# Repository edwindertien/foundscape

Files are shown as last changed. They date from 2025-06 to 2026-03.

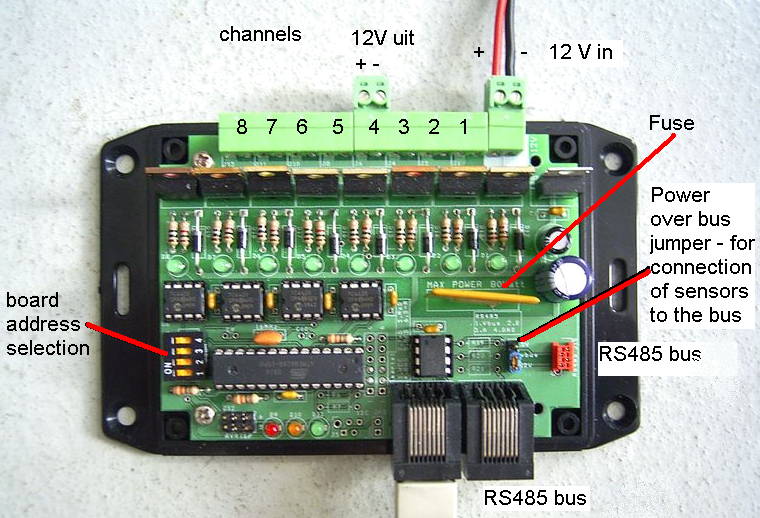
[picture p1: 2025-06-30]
atmegaDimmer/print.png

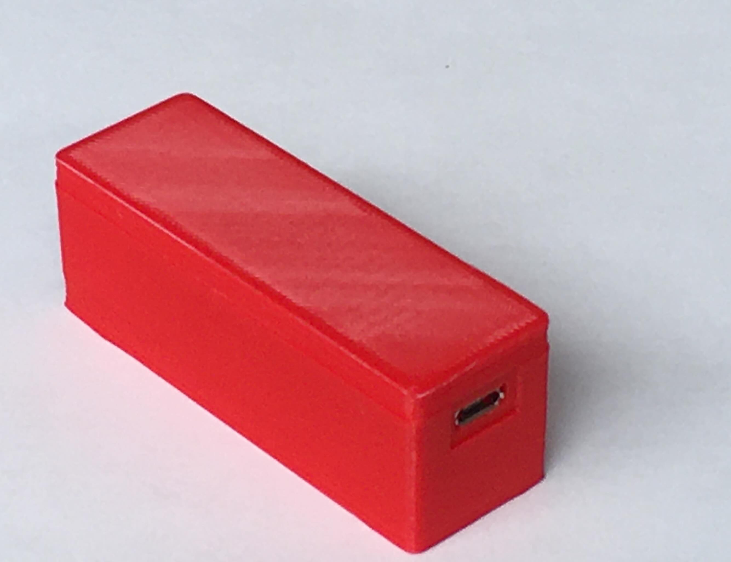
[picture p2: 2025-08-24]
images/RS485-midi-back.jpg

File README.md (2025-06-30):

# foundscape
midi control of things that tap and go boink. The basic structure consists of a midi-interface that takes data from Ableton (or similar) and sends events to 'dimmer cards' - being called like that because initially they mostly controlled LED light. 

Two behaviours exist on the main board right now which can be set using a small dip switch: either pulse-lenght or pwm duty cycle as third 'velocity' argument in a MIDI command. 

current version (still in operation) uses an ATmega328 (started out with the ATmega8 and then the ATmega88 in WinAVR. now it uses the Arduino environment). In the meantime a version has been made using Teensy, but has not been further pursued / produces (when Teensies were made of nonobtanium). On the wishlist a new version with pico

## modules
- [actuators](./actuators/) 3D printfiles for solenoid holders
- [atmegaDimmer](./atmegaDimmer/) first generation dimmer/control box, using RS485(dynamixel) protocol, using ATmega328
- [RS485adapter](./RS485adapter/) RS485 - midi interface using ATmega32U4 (Arduino micro, native USB)
- [teensyDimmer](./teensyDimmer/) update of dimmer/control box, using Teensy 4.0. build, not tested
- [picoDimmer](./picoDimmer/) new (to be designed) version of the dimmer/control box using RPI Pico 2040/2350

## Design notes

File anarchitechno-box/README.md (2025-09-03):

# foundscape electronics

## anarchitechno box (formerly known as 'pico dimmer')

The boxes are still called 'dimmer' since all channels can either be switched (solenoids, pneumatic valves) where the control parameter is a pulse duration (so short sharp tap or long, plungy tap - and everything in between) or a PWM value (used typically for LED brightness or motor velocity),

During a session at Koppelting (Amersfoort) in August 2025 we found that a very interesting additiion in just 'dimming' channels is also PWM (frequency) control and AWG / synthesis to make actuators sound even more. During the session the requirements below have been updated and start has been made with a new (schematic) design. 

On the wishlist for the next design (using for example the atmega version or the teensy version as starting point)

### power
- multiple voltages for output, would be nice to change per channel, but for now typically 1 output voltage (i.e. 12V) per channel is fine. It would be nice when the system can work on 12V, but also as low as 5V and at least at 24V
- 8 channels, individual control mode per channel for one-shot (solenoids, timing), PWM (frequency, duty cycle) and AWG (saw/sine/triangle/block/noise, frequency, phase, amplitude)
- polyfuse per channel, Fuse indicator
- 1 LED per channel (indication)
- flyback diodes per channel
- TVS, power supply protection, main fuse

not yet implemented but nice to have
- power monitoring (voltage / current)
- reverse voltage protection

For now the output section consisting of IRFZ44 and TC4423 has been working ok. Might be room to revise for newer, cheaper and SMD version. See if gate driver is necessary, but might be for higher switching frequencies. I checked other gate drivers, so far the 4427 seems a good (SMD) follow up with a good balance in price, performance and size

### power
Right now I tend to put in a Traco power TC2450 or similar to do the 12-24V to 5V conversion. Might be up for a change too. 

It wouls be very welcome to have galvanic separation between the power stage (12-24V side) and the logic side. The power consumption at the logic side is non-neglegible:
- pico (3.3V) - 20 mA? 
- OLED .. mA
- WS5500 .. mA
- USB Host -> 500mA

It might be best to build a 5Watt (1A) switching power supply or use a ready to go module. The TI 6505B uses a separate transformer (suggested, but need to be checked ) [wurth](https://octopart.com/750313974-wurth+electronics+midcom-49417564) and can go up to 5 Watt.

### galvanic separation
- using isolators it is important to separate the high/power (24V) side from the logic side. This means digital isolators as well as an isiolated 5V->5.5V supply. The USB Host needs 5V, the pico can do 5V->3.3V with its on-board converter

### brains
- pico (2W) - might be the standard board, or just the RP2040 or RP2350 chip + necessary peripherals
- OLED (small 32x128 pix) is very useful for menu, status info etc
- incremental encoder (3 switches) - pio code works fine. good for changing menu options
- simple basic LEDs on power and communication lines (so you can always check com, also when you are fiddeling with a menu), also from a distance. 
- WS8211 RGB leds (string), 1 per channel (channel mode selection) and communication status (per socket / unit)

### connection
- USB (midi, serial)  -> existing USB micro
- USB Host (midi, gamepad, HID) -> add USB A socket. Think about necessary series resistors and power components. 
- RS485 (DMX: neutrix 3/5 pin, 'dynamixel' bus) -> 3way(A, B, GND) and 4way (A, B, Power, GND) jst socket. For (my) RJ45 and a neutrik socket we can make an adapter? Or have the RJ45 system since it is so easy to stack through.. 
- ethernet: WSD5500 + socket + mag
- MIDI: old fashioned 5-pin DIN midi (CNY138 optocoupler) (can also be adapter cable from 5-way jst socket)
- A pico could in theory also do everything WIFI / Bluetooth / BLE wise. .. 
- HW sync input (optocoupler?)

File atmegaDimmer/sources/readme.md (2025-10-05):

Install the hardware (ottantotto) by copying the 'hardware' dir to arduino's sketchfolder
the boards mainly use ATmega88, programmed by an AVR-ISP (so no bootloader)

Alternatively an ATmega328p can be used, with the 'normal' bootloader for Arduino Uno. This means that for a first go still the AVR-ISP has to be used. Since there is no serial port on the dimmer, it does not make much sense using the bootloader anyway :)

The dimmerboard source can do soft-pwm on 8 outputs, as well as one-shot control (for valves / solenoids)

Four jumpers can set different aspects. The first two jumpers (closest to the output side) select the channel the boards respond to (so four channels can be selected). The third jumper switches between one-shot (time) and pwm mode (off: pwm, on: one-shot). the last (fourth) jumper, closest to the input side of the board, slects high (1000000) or low (115200) baudrate. off: 115200, on: 1000000

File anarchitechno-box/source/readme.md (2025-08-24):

#### Readme.md ####

### V1.0 

These boards have been equipped with the PCA9685 which can do PWM low enough to drive servos directly. The 10 pin IDC socket next to the Pico has 8 GPIO pins of which 3 middle ones are also used for the incremental encoder

### V2.0

The V2.0 has additional 4-way JST sockets for hooking up additional IO (the same GPIO pins mentioned above) such as two H-bridges. 

Instead of the PCA9685 the PCA9635 is used which has a default 'HIGH' state so the Relays do not turn on during powerup. 

A L9110S driver has been added in the schematic to drive the high-side power for the relays, but this has no effect (and, in error, only allows one relay board to be powered simultanously. Apparently the state where both outputs are high does not exist and the component does not follow its datasheet :-(  )

eventually a wire of player1 is not connected to the linking resistors (lowest resistor on the PCB) - this has been adjusted with a wire.

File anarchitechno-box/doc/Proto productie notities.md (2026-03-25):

- Voor zelf getekende onderdelen checken of JLC snapt waar pin 1 zit...
- De fonts van 'Foundscape' en 'Anarchitechbox' heb ik niet op MacOS. Staan deze teksten op silkscreen top/bottom nog netjes uitgelijnd?

BOM aantekeningen:
- U11, U12, U20, U21: DRV8245S of DRV8245P variant hebben we nodig, in PWP package. JLC heeft alleen DRV8245SQPWPRQ1, echter beperkt voorraadig..
- U4: RMC20452T is duur & niet op voorraad bij JLC
- U18: ADPL54203ES8E is niet op voorraad bij JLC
- U19: 750311564 trafo ook zelf solderen? (in geval flyback niet werkt, dan hoeven we andere borden niet zwaar te modificeren)

- De meeste passives zijn gekozen uit basic parts en hebben al onderdeel nrs.
- Een enkel onderdeel is Extended vanwege component waarde en/of package.
- Sommige passives zijn niet aangewezen, hopelijk pakt JLC dit automatisch uit basic parts lib.

- Wat rekent JLC voor TH assemblage?
- Overwegen TH mechanische onderdelen zelf te plaatsen? J3 J4 J5 J6 J7 J8 J11 J12 CN1 CN2 SW2, en eventueel J1?
- Overwegen TH capaciators zelf te plaatsen? C38, C39, C44, C45, C78, C79, C84, C85

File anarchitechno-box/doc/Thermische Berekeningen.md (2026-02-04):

## Thermische berekening IRFZ44

ATMEGAdimmer gebruikt IRFZ44 MOSFETs. Deze worden met 12V aangestuurd, en hebben 28mOhm Rds(on) bij Vgs=10V. 

De thermische weerstand van een TO-220 "free standing" is 62C/W. Met Tj(max)=175C en Ta(max)=35C hebben we: P(max)=(175 - 35)/62 = 2.26W. Met 28mOhm en P=I^2*R => I^2=80.7A^2 => Imax=8.98A

Dit is de maximum DC stroom. Met PWM wordt het maximum wegens schakelverliezen nog (flink) lager. Maar zo'n berekening is wat lastiger en laat ik even achterwege.
Ook de recirculation stroom is niet meegenomen. Onduidelijk van schema is hoe die oorspronkelijk werd opgevangen.

## Thermische berekening DRV8245

Dit is een H-brug, wat extra mogelijkheden geeft wat betreft aansturing van solenoids en motors. 

In een H-brug configuratie betekent het wel dat de stroom door 2 transistors loopt. Maar dit staat gelijk aan 2 kanalen enkel high-side aansturen.

De low-side en high-side transistor heeft een Rds(on) van 40mOhm (HTSSOP) of 32mOhm (VQFN).

Tj(max)=150C
Ta(max)=45C (alle verliezen gaan 1 gezamelijke PCB in, dus deze schat ik iets hoger in)
Rj-a=27.7C/W (HTSSOP package), of 41.3C/W (VQFN package)

We gebruiken de HTSSOP package, want:

P(max)=(150-45)/27.7=3.8W
P=I^2*R => I^2=94.8A^2 => 9.7A 1-ch
Omdat er 2 actieve transistors in 1 package zitten, mag eigenlijk elke transistor maar 1.9W dissiperen. Dan:
I^2 = 47.7A^2 => 6.88A 2-ch (of H-brug)

Voor VQFN:
P(max)=(150-45)/41.3=2.54W
I^2 = 79.4A^2 => 8.91A 1-ch, en 6.32A 2-ch

De datasheet geeft pessimistischere waarden omdat deze met 85C ambient temperatuur rekent. Wel staat er een model in voor 10-sec belastingen alsook in combinatie met 20kHz PWM.

Daarin zeggen ze:
- DC+PWM: 4.5A
- 10sec+PWM: 7.4A
- DC+no PWM: 5.4A
- 10sec+no PWM: 8.4A
- 0.1sec+no PWM: 16.1A

20kHz PWM kost dus 12-17% van de maximale stroom capaciteit.

We kunnen eventueel [https://www.tinytronics.nl/en/mechanics-and-actuators/parts/cooling-elements/aluminum-heatsink-7x7x7mm-with-adhesive](met heatsinks) en een 140mm fan de thermische weerstand (flink) verlagen..

Betreffende recirculation:
 
In geval van een high-side only power switch, is het verstandig om een losse vrijloop Schottky diode toe te voegen. Ik verwacht deze een lagere VF heeft dan de DRV8245.
In geval van H-brug aansturing is er keuze tussen fast en short decay, respectievelijk open-circuit (stroom wordt door body diodes van MOSFETs gejaagd) of short-circuit (zo min mogelijk serie verliezen).

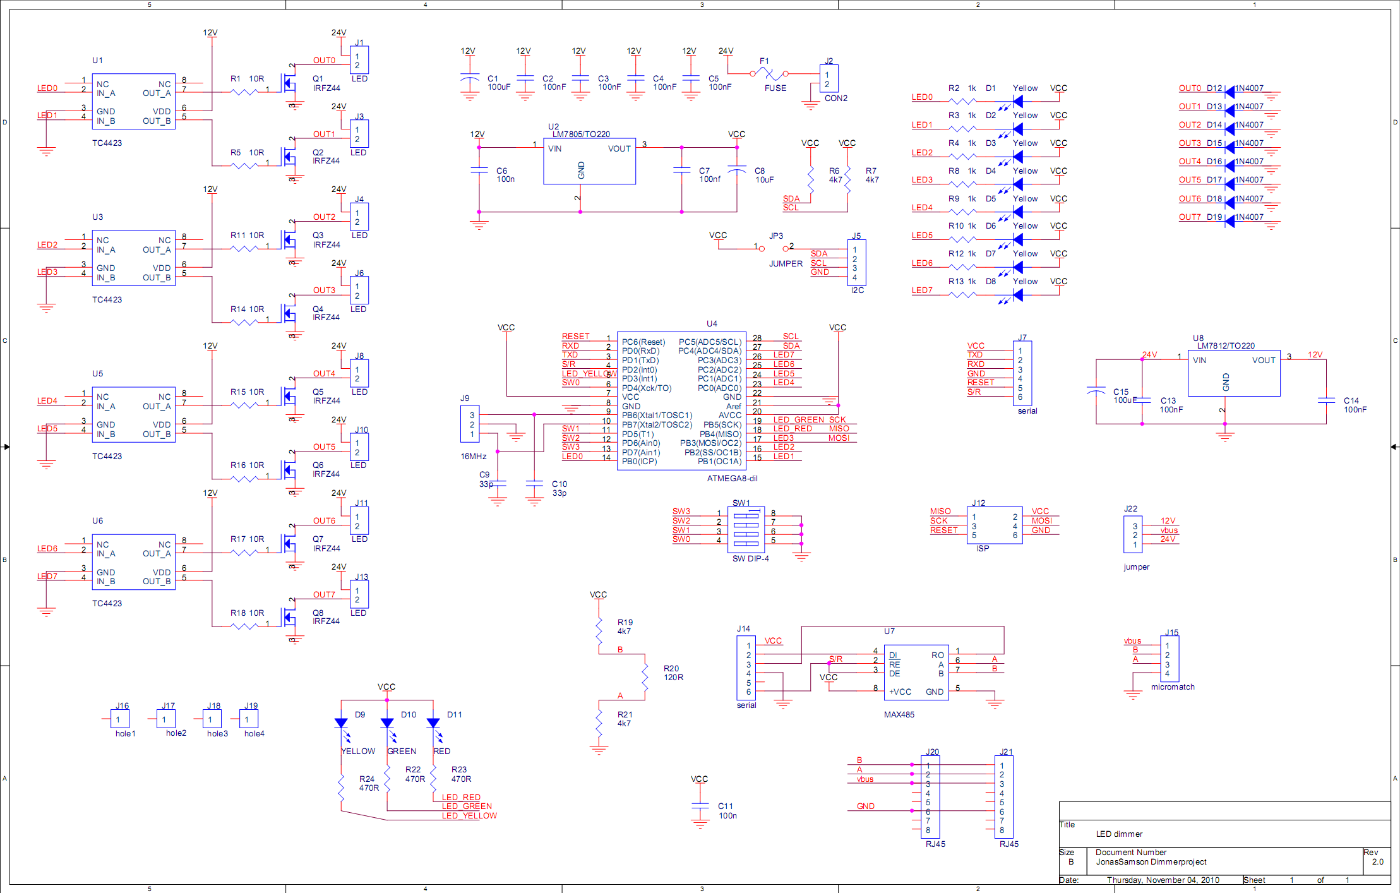
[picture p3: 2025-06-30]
atmegaDimmer/electronics/schematic/leddimmerv3schematic.png

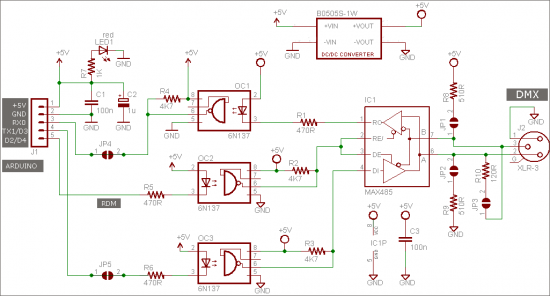
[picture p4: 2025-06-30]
anarchitechno-box/resources/6-DMX-Shield-v1-Schematic-550x296-2691643487.png

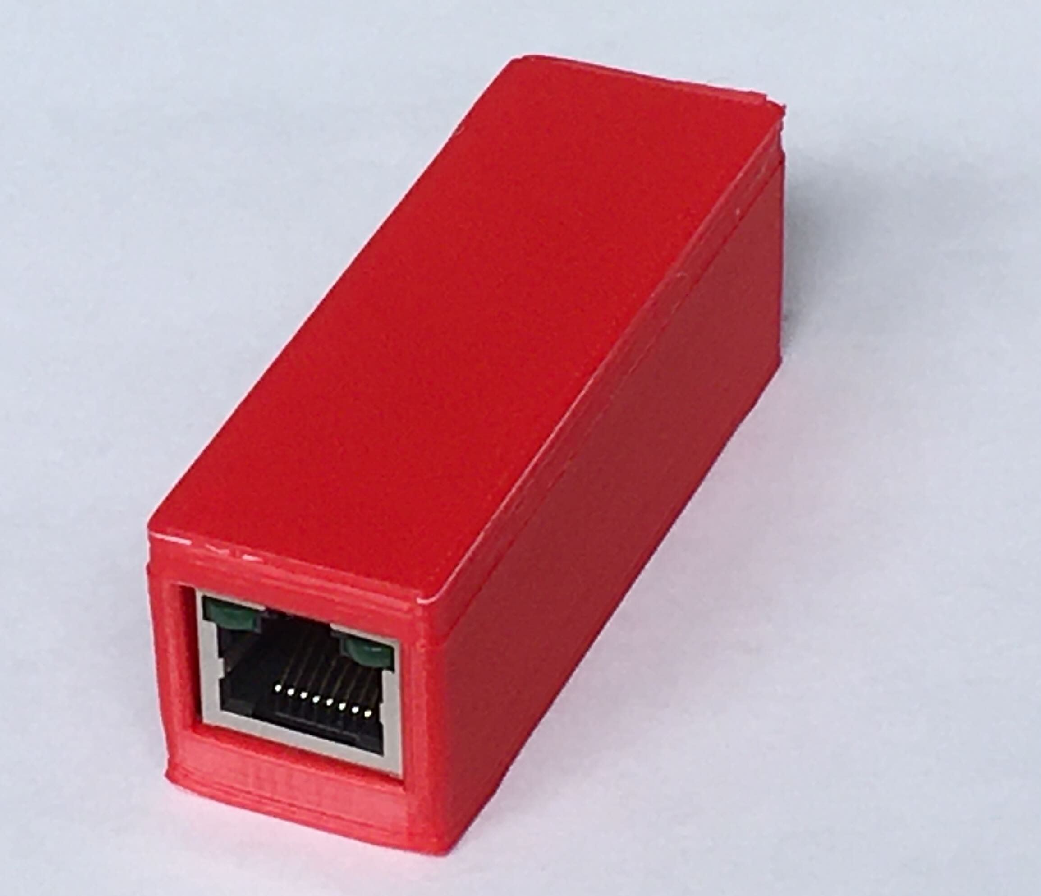
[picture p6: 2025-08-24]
images/RS485-midi.jpg

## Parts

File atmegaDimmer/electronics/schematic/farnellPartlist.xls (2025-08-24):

part, value | farnell | comment | n | part | n total 10pc
100uF | 9693670 (http://nl.farnell.com/panasonic/eca1vm101/capacitor-100uf-35v/dp/9693670) | 35V | 1 | 9693670 | 10
100nf 5.08 | 1216445 (https://nl.farnell.com/jsp/search/productdetail.jsp?SKU=1216445) |  | 10 | 1216445 | 100
10uF | 9452281 (https://nl.farnell.com/jsp/search/productdetail.jsp?SKU=9452281) | 35V | 1 | 9452281 | 10
LED YELLOW 3mm | 1003198 (https://nl.farnell.com/jsp/search/productdetail.jsp?SKU=1003198) |  | 1 | 1003198 | 10
LED GREEN 3mm | 1142502 (https://nl.farnell.com/jsp/search/productdetail.jsp?SKU=1142502) |  | 9 | 1142502 | 90
LED RED 3mm | 1142517 (https://nl.farnell.com/jsp/search/productdetail.jsp?SKU=1142517) |  | 1 | 1142517 | 10
1N4007 | 9565051 (https://nl.farnell.com/jsp/search/productdetail.jsp?SKU=9565051) |  | 8 | 9565051 | 80
FUSE 9A | 9350110 (https://nl.farnell.com/jsp/search/productdetail.jsp?SKU=9350110) |  | 1 | 9350110 | 10
3.81mm 2WAY socket | 3704725 (https://nl.farnell.com/jsp/search/productdetail.jsp?SKU=3704725) |  | 1 | 3704725 | 10
16MHz resonator | 1448129 (https://nl.farnell.com/jsp/search/productdetail.jsp?SKU=1448129) |  | 1 | 1448129 | 10
4WAY micromatch socket | 148507 (https://nl.farnell.com/jsp/search/productdetail.jsp?SKU=148507) |  | 2 | 148507 | 20
RJ45 socket | 3938360 (https://nl.farnell.com/jsp/search/productdetail.jsp?SKU=3938360) |  | 2 | 3938360 | 20
IRFZ44 N-MOSFET | 8650250 (https://nl.farnell.com/jsp/search/productdetail.jsp?SKU=8650250) |  | 8 | 8650250 | 80
10R | 9339035 (https://nl.farnell.com/jsp/search/productdetail.jsp?SKU=9339035) |  | 8 | 9339035 | 80
1k | 9339051 (https://nl.farnell.com/jsp/search/productdetail.jsp?SKU=9339051) |  | 8 | 9339051 | 80
4k7 | 9338829 (https://nl.farnell.com/jsp/search/productdetail.jsp?SKU=9338829) |  | 2 | 9338829 | 20
330R | 9339418 (https://nl.farnell.com/jsp/search/productdetail.jsp?SKU=9339418) |  | 3 | 9339418 | 30
SW DIP-4 | 9471600 (https://nl.farnell.com/jsp/search/productdetail.jsp?SKU=9471600) |  | 1 | 9471600 | 10
TC4423 | 1439740 (https://nl.farnell.com/jsp/search/productdetail.jsp?SKU=1439740) |  | 4 | 1439740 | 40
LM7805/TO220 | 1211135 (https://nl.farnell.com/jsp/search/productdetail.jsp?SKU=1211135) |  | 1 | 1211135 | 10
ATMEGA8-dil | 1661728 (https://nl.farnell.com/jsp/search/productdetail.jsp?SKU=1661728) | (14 per tube) | 1 | 1661728 | 10
MAX485 | 9561323 (https://nl.farnell.com/jsp/search/productdetail.jsp?SKU=9561323) |  | 1 | 9561323 | 10
3.81mm 8WAY socket | 3704774 (https://nl.farnell.com/jsp/search/productdetail.jsp?SKU=3704774) |  | 2 | 3704774 | 20
3.81mm 8WAY PLUG | 1717053 (https://nl.farnell.com/jsp/search/productdetail.jsp?SKU=1717053) |  | 2 | 1717053 | 20
3.81mm 2WAY plug | 3704907 (https://nl.farnell.com/jsp/search/productdetail.jsp?SKU=3704907) |  | 2 | 3704907 | 20
ic socket 8 way | 1101345 (https://nl.farnell.com/jsp/search/productdetail.jsp?SKU=1101345) |  | 5 | 1101345 | 50
470uF | 1692322 (https://nl.farnell.com/jsp/search/productdetail.jsp?SKU=1692322) |  | 1 | 1692322 | 10
28way ic | 1103850 (https://nl.farnell.com/jsp/search/productdetail.jsp?SKU=1103850) |  | 1 | 1103850 | 10
power socket 2.1mm | 1217037 (https://nl.farnell.com/jsp/search/productdetail.jsp?SKU=1217037) |  | 1 | 1217037 | 10
power plug 2.1mm | 1217034 (https://nl.farnell.com/jsp/search/productdetail.jsp?SKU=1217034) |  | 1 | 1217034 | 10
pin header 36 | 9729062 (https://nl.farnell.com/jsp/search/productdetail.jsp?SKU=9729062) |  | 1 | 9729062 | 10
micromatch plug 4 | 149032 (https://nl.farnell.com/jsp/search/productdetail.jsp?SKU=149032) |  | 2 | 149032 | 20

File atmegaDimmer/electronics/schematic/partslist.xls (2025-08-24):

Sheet: Big partlist
Big Part List FARNELL |  |  | Dimmerboard |  |  | Ottantotto |  |  | RS485controller
part, value | farnell | comment | n | part | n total | n | part | n total | n | part | n total
100uF | 9693670 (http://nl.farnell.com/panasonic/eca1vm101/capacitor-100uf-35v/dp/9693670) | 35V | 2 | 9693670 | 20 | 1 | 9693670 | 10 | 1 | 9693670 | 10
100nf 5.08 | 1216445 (https://nl.farnell.com/jsp/search/productdetail.jsp?SKU=1216445) |  | 10 | 1216445 | 100 |  | 1216445 | 0 | 5 | 1216445 | 50
10uF | 9452281 (https://nl.farnell.com/jsp/search/productdetail.jsp?SKU=9452281) | 35V | 1 | 9452281 | 10 | 1 | 9452281 | 10 | 1 | 9452281 | 10
33p | 9339043 (http://nl.farnell.com/multicomp/mcf-0-25w-100r/resistor-0-25w-5-100r/dp/9339043) |  |  | 9339043 | 0 |  | 9339043 | 0 |  | 9339043 | 0
LED YELLOW 3mm | 1003198 (https://nl.farnell.com/jsp/search/productdetail.jsp?SKU=1003198) |  | 1 | 1003198 | 10 | 1 | 1003198 | 10 | 1 | 1003198 | 10
LED GREEN 3mm | 1142502 (https://nl.farnell.com/jsp/search/productdetail.jsp?SKU=1142502) |  | 9 | 1142502 | 90 | 2 | 1142502 | 20 | 1 | 1142502 | 10
LED RED 3mm | 1142517 (https://nl.farnell.com/jsp/search/productdetail.jsp?SKU=1142517) |  | 1 | 1142517 | 10 | 1 | 1142517 | 10 | 1 | 1142517 | 10
1N4007 | 9565051 (https://nl.farnell.com/jsp/search/productdetail.jsp?SKU=9565051) |  | 8 | 9565051 | 80 | 1 | 9565051 | 10 | 1 | 9565051 | 10
FUSE 9A | 9350110 (https://nl.farnell.com/jsp/search/productdetail.jsp?SKU=9350110) |  | 1 | 9350110 | 10 |  | 9350110 | 0 |  | 9350110 | 0
3.81mm 2WAY socket | 3704725 (https://nl.farnell.com/jsp/search/productdetail.jsp?SKU=3704725) |  | 1 | 3704725 | 10 |  | 3704725 | 0 |  | 3704725 | 0
16MHz resonator | 1448129 (https://nl.farnell.com/jsp/search/productdetail.jsp?SKU=1448129) |  | 1 | 1448129 | 10 | 1 | 1448129 | 10 | 1 | 1448129 | 10
4WAY micromatch socket | 148507 (https://nl.farnell.com/jsp/search/productdetail.jsp?SKU=148507) |  | 2 | 148507 | 20 |  | 148507 | 0 | 2 | 148507 | 20
RJ45 socket | 3938360 (https://nl.farnell.com/jsp/search/productdetail.jsp?SKU=3938360) |  | 2 | 3938360 | 20 |  | 3938360 | 0 | 2 | 3938360 | 20
IRFZ44 N-MOSFET | 8650250 (https://nl.farnell.com/jsp/search/productdetail.jsp?SKU=8650250) |  | 8 | 8650250 | 80 |  | 8650250 | 0 |  | 8650250 | 0
10R | 9339035 (https://nl.farnell.com/jsp/search/productdetail.jsp?SKU=9339035) |  | 8 | 9339035 | 80 |  | 9339035 | 0 |  | 9339035 | 0
1k | 9339051 (https://nl.farnell.com/jsp/search/productdetail.jsp?SKU=9339051) |  | 8 | 9339051 | 80 |  | 9339051 | 0 |  | 9339051 | 0
4k7 | 9338829 (https://nl.farnell.com/jsp/search/productdetail.jsp?SKU=9338829) |  | 2 | 9338829 | 20 |  | 9338829 | 0 | 2 | 9338829 | 20
120R | 9339116 (https://nl.farnell.com/jsp/search/productdetail.jsp?SKU=9339116) |  |  | 9339116 | 0 |  | 9339116 | 0 |  | 9339116 | 0
330R | 9339418 (https://nl.farnell.com/jsp/search/productdetail.jsp?SKU=9339418) |  | 3 | 9339418 | 30 | 4 | 9339418 | 40 | 3 | 9339418 | 30
SW DIP-4 | 9471600 (https://nl.farnell.com/jsp/search/productdetail.jsp?SKU=9471600) |  | 1 | 9471600 | 10 |  | 9471600 | 0 | 1 | 9471600 | 10
TC4423 | 1439740 (https://nl.farnell.com/jsp/search/productdetail.jsp?SKU=1439740) |  | 4 | 1439740 | 40 |  | 1439740 | 0 |  | 1439740 | 0
LM7805/TO220 | 1211135 (https://nl.farnell.com/jsp/search/productdetail.jsp?SKU=1211135) |  | 1 | 1211135 | 10 | 1 | 1211135 | 10 | 1 | 1211135 | 10
ATMEGA8-dil | 1661728 (https://nl.farnell.com/jsp/search/productdetail.jsp?SKU=1661728) | (14 per tube) | 1 | 1661728 | 10 | 1 | 1661728 | 10 | 1 | 1661728 | 1
MAX485 | 9561323 (https://nl.farnell.com/jsp/search/productdetail.jsp?SKU=9561323) |  | 1 | 9561323 | 10 |  | 9561323 | 0 | 1 | 9561323 | 10
3.81mm 8WAY socket | 3704774 (https://nl.farnell.com/jsp/search/productdetail.jsp?SKU=3704774) |  | 2 | 3704774 | 20 |  | 3704774 | 0 |  | 3704774 | 0
3.81mm 8WAY PLUG | 1717053 (https://nl.farnell.com/jsp/search/productdetail.jsp?SKU=1717053) |  | 2 | 1717053 | 20 |  | 1717053 | 0 |  | 1717053 | 0
3.81mm 2WAY plug | 3704907 (https://nl.farnell.com/jsp/search/productdetail.jsp?SKU=3704907) |  | 2 | 3704907 | 20 |  | 3704907 | 0 |  | 3704907 | 0
ic socket 14 way | 1182586 (https://nl.farnell.com/jsp/search/productdetail.jsp?SKU=1182586) | tube 34 |  | 1182586 | 0 | 2 | 1182586 | 20 | 0 | 1182586 | 0
ic socket 16 way | 1182587 (https://nl.farnell.com/jsp/search/productdetail.jsp?SKU=1182587) | tube 34 |  | 1182587 | 0 | 1 | 1182587 | 10 |  | 1182587 | 0
ic socket 8 way | 1101345 (https://nl.farnell.com/jsp/search/productdetail.jsp?SKU=1101345) |  | 5 | 1101345 | 50 |  | 1101345 | 0 | 1 | 1101345 | 10
470uF | 1692322 (https://nl.farnell.com/jsp/search/productdetail.jsp?SKU=1692322) |  |  | 1692322 | 0 |  | 1692322 | 0 |  | 1692322 | 0
harting RJ45 socket | 1170278 (https://nl.farnell.com/jsp/search/productdetail.jsp?SKU=1170278) | socket |  | 1170278 | 0 |  | 1170278 | 0 |  | 1170278 | 0
harting RJ 45 plug | 1106815 (https://nl.farnell.com/jsp/search/productdetail.jsp?SKU=1106815) | plug |  | 1106815 | 0 |  | 1106815 | 0 |  | 1106815 | 0
motion sensor A31112 | 1373710 (https://nl.farnell.com/jsp/search/productdetail.jsp?SKU=1373710) | panasonic |  | 1373710 | 0 |  | 1373710 | 0 |  | 1373710 | 0
distance sens | 1618432 (https://nl.farnell.com/jsp/search/productdetail.jsp?SKU=1618432) | sharp |  | 1618432 | 0 |  | 1618432 | 0 |  | 1618432 | 0
plug RJ45 crimp | 1712387 (https://nl.farnell.com/jsp/search/productdetail.jsp?SKU=1712387) |  |  | 1712387 | 0 |  | 1712387 | 0 |  | 1712387 | 0
28way ic | 1103850 (https://nl.farnell.com/jsp/search/productdetail.jsp?SKU=1103850) |  | 1 | 1103850 | 10 |  | 1103850 | 0 | 1 | 1103850 | 10
power socket 2.1mm | 1217037 (https://nl.farnell.com/jsp/search/productdetail.jsp?SKU=1217037) |  | 1 | 1217037 | 10 | 1 | 1217037 | 10 | 1 | 1217037 | 10
power plug 2.1mm | 1217034 (https://nl.farnell.com/jsp/search/productdetail.jsp?SKU=1217034) |  | 1 | 1217034 | 10 | 1 | 1217034 | 10 | 1 | 1217034 | 10
pin header 36 | 9729062 (https://nl.farnell.com/jsp/search/productdetail.jsp?SKU=9729062) |  | 1 | 9729062 | 10 | 2 | 9729062 | 20 | 1 | 9729062 | 10
dsub9 solder | 1084678 (https://nl.farnell.com/jsp/search/productdetail.jsp?SKU=1084678) |  |  | 1084678 | 0 | 1 | 1084678 | 10 |  | 1084678 | 0
micromatch plug 4 | 149032 (https://nl.farnell.com/jsp/search/productdetail.jsp?SKU=149032) |  | 2 | 149032 | 20 |  | 149032 | 0 | 2 | 149032 | 20
capacitor 1uF | 9452524 (https://nl.farnell.com/jsp/search/productdetail.jsp?SKU=9452524) |  |  | 9452524 | 0 | 5 | 9452524 | 50 |  | 9452524 | 0
max232 | 9589805 (https://nl.farnell.com/jsp/search/productdetail.jsp?SKU=9589805) |  |  | 9589805 | 0 | 1 | 9589805 | 10 |  | 9589805 | 0
100nF 2.54 | 1216444 (https://nl.farnell.com/jsp/search/productdetail.jsp?SKU=1216444) |  |  | 1216444 | 0 | 5 | 1216444 | 50 |  | 1216444 | 0
IR receiver 36khz | 4913061 (https://nl.farnell.com/jsp/search/productdetail.jsp?SKU=4913061) |  |  | 4913061 | 0 |  | 4913061 | 0 |  | 4913061 | 0
IR emitter | 1045378 (https://nl.farnell.com/jsp/search/productdetail.jsp?SKU=1045378) |  |  | 1045378 | 0 |  | 1045378 | 0 |  | 1045378 | 0
speaker, mylar cone | 1300021 (https://nl.farnell.com/jsp/search/productdetail.jsp?SKU=1300021) |  |  | 1300021 | 0 |  | 1300021 | 0 |  | 1300021 | 0
1000 uF panasonic | 9692738 (https://nl.farnell.com/jsp/search/productdetail.jsp?SKU=9692738) |  |  | 9692738 | 0 | 1 | 9692738 | 10 |  | 9692738 | 0
micromatch socket 6 | 148519 (https://nl.farnell.com/jsp/search/productdetail.jsp?SKU=148519) |  |  | 148519 | 0 |  | 148519 | 0 |  | 148519 | 0
2950 - 3.3v regulater TO92 | 1652319 (https://nl.farnell.com/jsp/search/productdetail.jsp?SKU=1652319) |  |  | 1652319 | 0 |  | 1652319 | 0 |  | 1652319 | 0
SD card socket | 9186174 (https://nl.farnell.com/jsp/search/productdetail.jsp?SKU=9186174) |  |  | 9186174 | 0 |  | 9186174 | 0 |  | 9186174 | 0
FUSE 1.6A (small) | 1822235 (http://nl.farnell.com/littelfuse/30r160uu/polyfuse-ptc-radial-1-6a/dp/1822235) |  |  | 1822235 | 0 |  | 1822235 | 0 | 1 | 1822235 | 10
100R | 9339043 (http://nl.farnell.com/multicomp/mcf-0-25w-100r/resistor-0-25w-5-100r/dp/9339043) |  |  | 9339043 | 0 |  | 9339043 | 0 | 1 | 9339043 | 10
10k | 9339060 (http://nl.farnell.com/multicomp/mcf-0-25w-10k/resistor-0-25w-5-10k/dp/9339060) |  |  | 9339060 | 0 | 1 | 9339060 | 10 |  | 9339060 | 0
78LM12 | 1467365 (http://nl.farnell.com/fairchild-semiconductor/lm7812ct/v-reg-adj/dp/1467365) |  |  | 1467365 | 0 |  | 1467365 | 0 |  | 1467365 | 0
33pf | 1141761 (http://nl.farnell.com/vishay/k330j15c0gf53l2/capacitor-33pf-50v/dp/1141761) | if not resonator | 2 | 1141761 | 20 |  | 1141761 | 0 | 2 | 1141761 | 20
 |  |  |  | 0 | 0 |  | 0 | 0 |  | 0 | 0
 |  |  |  | 0 | 0 |  | 0 | 0 |  | 0 | 0

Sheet: dimmerboard
Dimmerboard | 10x
9693670 | 20
1216445 | 100
9452281 | 10
1003198 | 10
1142502 | 90
1142517 | 10
9565051 | 80
9350110 | 10
3704725 | 10
1448129 | 10
148507 | 20
3938360 | 20
8650250 | 80
9339035 | 80
9339051 | 80
9338829 | 20
9339418 | 30
9471600 | 10
1439740 | 40
1211135 | 10
1661728 | 1
9561323 | 10
3704774 | 20
1717053 | 20
3704907 | 20
1101345 | 50
1103850 | 10
1217037 | 10
1217034 | 10
9729062 | 10
149032 | 20

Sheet: rs485controller
RS485controller | 10x
9693670 | 10
1216445 | 50
9452281 | 10
1003198 | 10
1142502 | 10
1142517 | 10
9565051 | 10
1448129 | 10
148507 | 20
3938360 | 20
9338829 | 20
9339418 | 30
9471600 | 10
1211135 | 10
1661728 | 1
9561323 | 10
1101345 | 10
1103850 | 10
1217037 | 10
1217034 | 10
9729062 | 10
149032 | 20
1822235 (http://nl.farnell.com/littelfuse/30r160uu/polyfuse-ptc-radial-1-6a/dp/1822235) | 10
9339043 | 10

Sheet: ottantotto
ottantotto | 10x
9693670 | 10
9452281 | 10
1003198 | 10
1142502 | 20
1142517 | 10
9565051 | 10
1448129 | 10
9339418 | 40
1211135 | 10
1661728 | 1
1182586 | 20
1182587 | 10
1217037 | 10
1217034 | 10
9729062 | 20
9452524 | 50
9589805 | 10
1216444 | 50
9692738 | 10
9339060 | 10
1084678 | 10

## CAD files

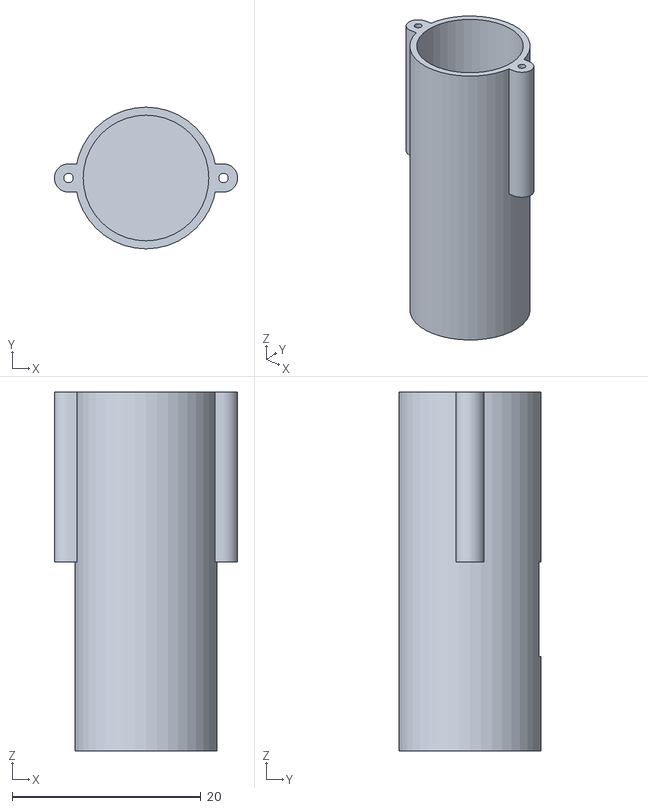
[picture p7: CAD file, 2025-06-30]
actuators/pull-solenoid/hitter.stl
19.4 x 15.0 x 38.0

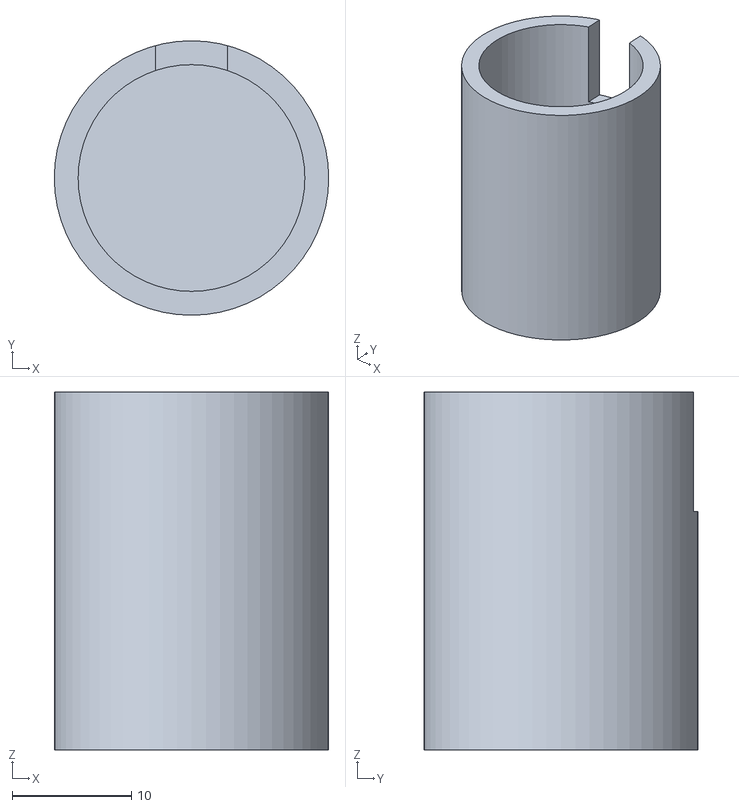
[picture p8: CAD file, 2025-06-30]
actuators/push solenoid/tapperdaiper.stl
23.0 x 23.0 x 30.0

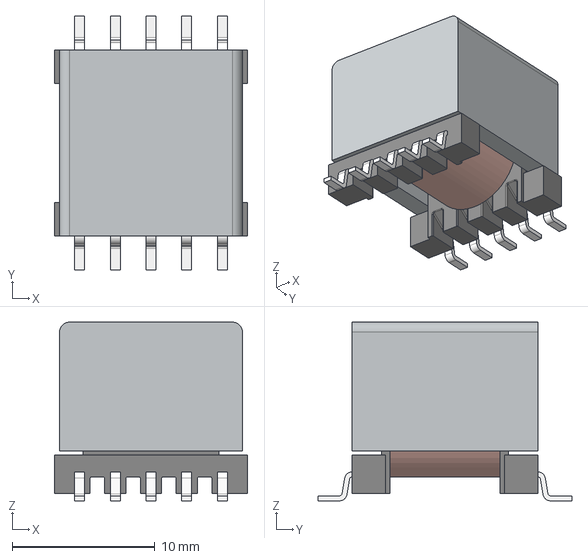
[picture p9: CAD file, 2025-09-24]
anarchitechno-box/kicad/3d/T_Wurth_WE-FB-EP13_16.36.step
13.5 x 17.8 x 12.5 mm

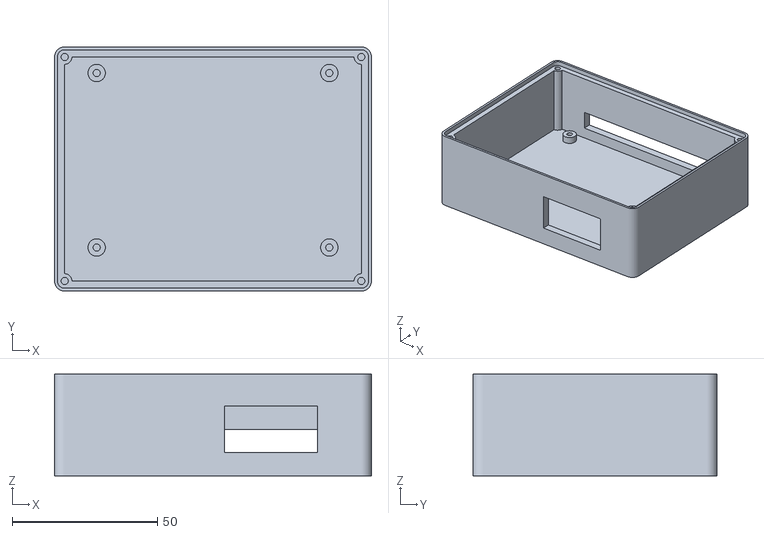
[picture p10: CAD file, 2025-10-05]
atmegaDimmer/box/dimmerbox.stl
109.0 x 84.0 x 35.0

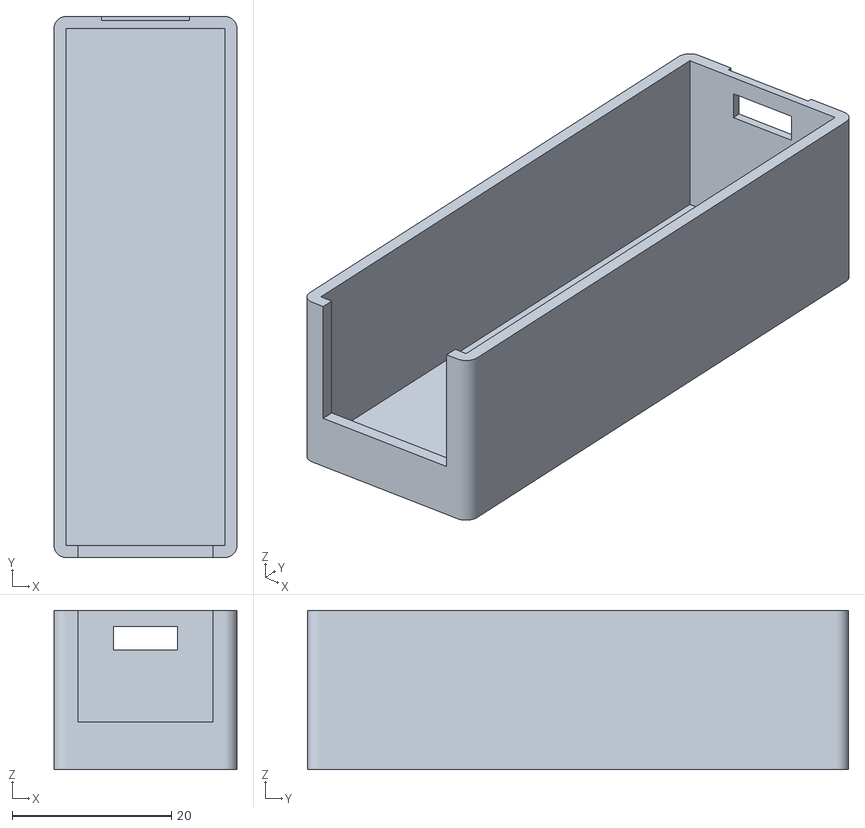
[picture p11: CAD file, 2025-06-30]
microRS485-MIDI/box/box.stl
23.0 x 68.0 x 20.0

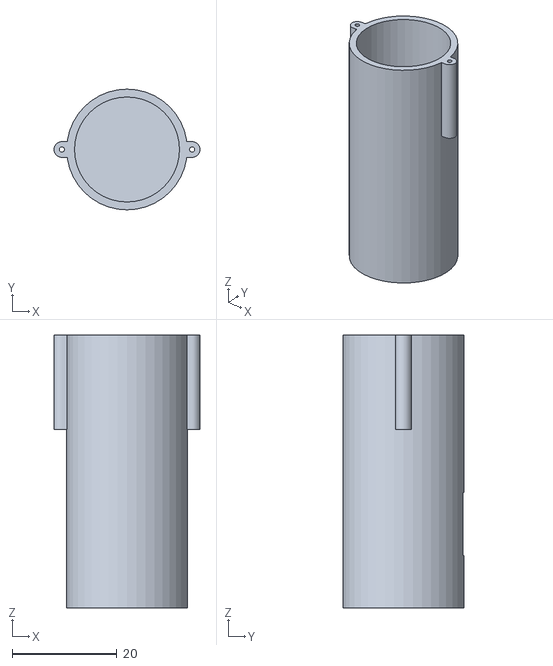
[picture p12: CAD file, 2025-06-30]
actuators/pull-solenoid/hitterLarge.stl
27.8 x 23.0 x 52.0

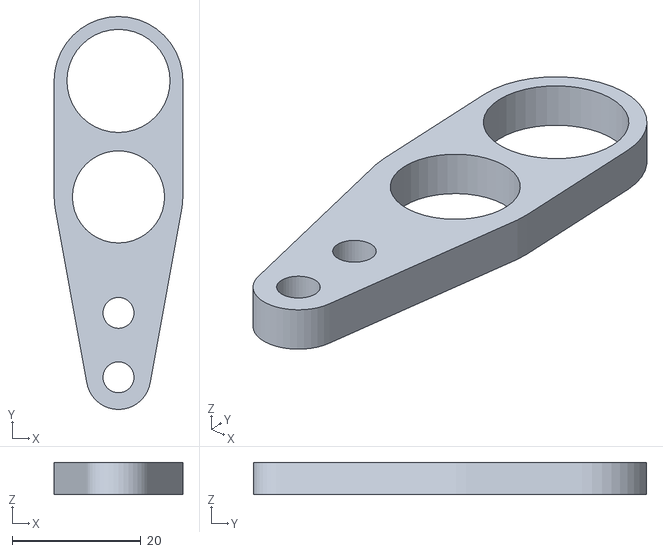
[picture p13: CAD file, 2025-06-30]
actuators/push solenoid/holder.stl
20.0 x 61.0 x 5.00

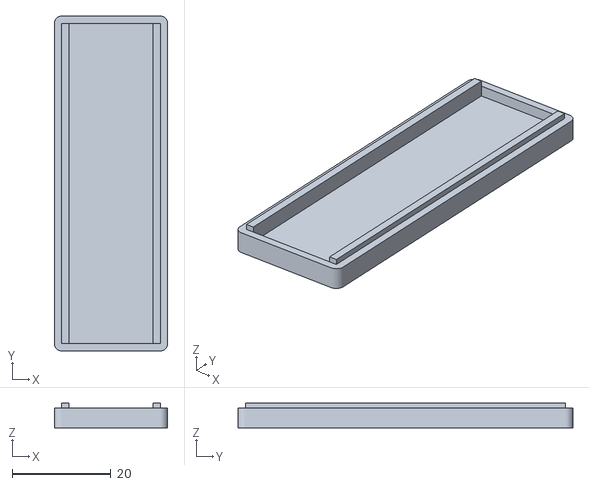
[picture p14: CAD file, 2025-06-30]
microRS485-MIDI/box/lid.stl
23.0 x 68.0 x 5.00

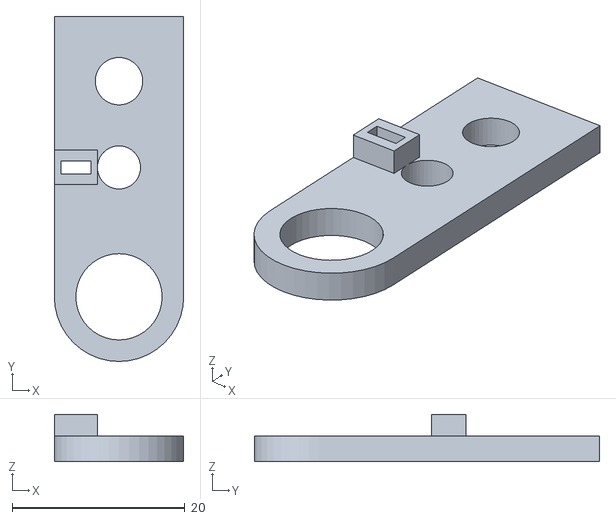
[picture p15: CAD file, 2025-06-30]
actuators/pull-solenoid/plate.stl
15.0 x 40.0 x 5.50

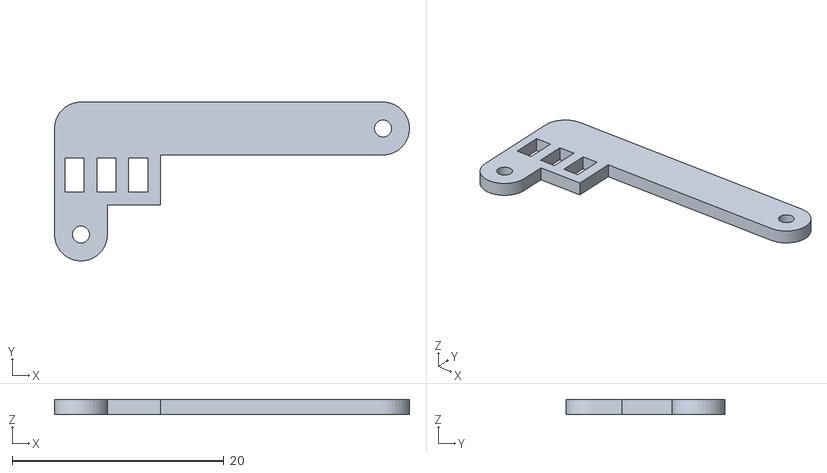
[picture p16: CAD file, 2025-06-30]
actuators/pull-solenoid/link_small.stl
33.5 x 15.0 x 1.40

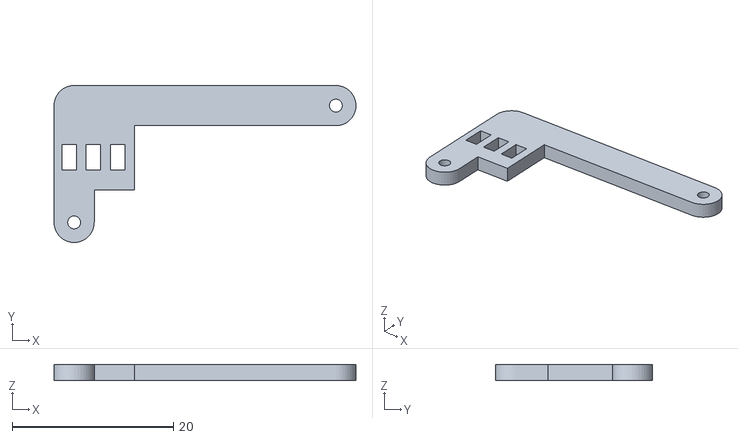
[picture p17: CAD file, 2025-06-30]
actuators/pull-solenoid/link.stl
37.5 x 19.5 x 2.00

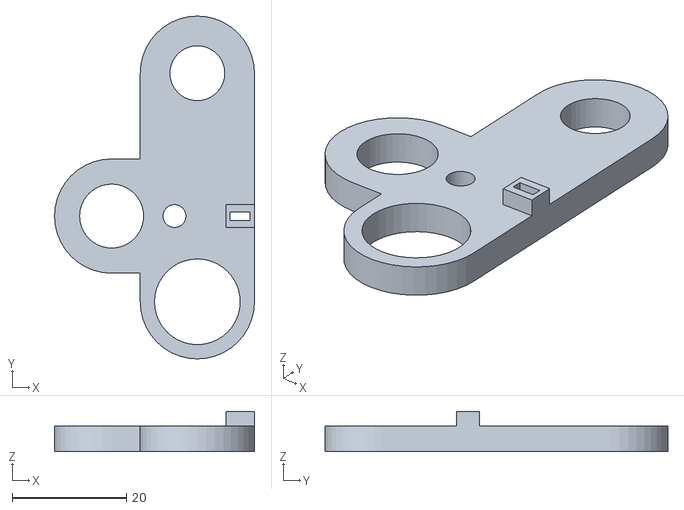
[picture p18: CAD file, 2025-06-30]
actuators/pull-solenoid/plate_new_large.stl
35.0 x 60.0 x 7.00

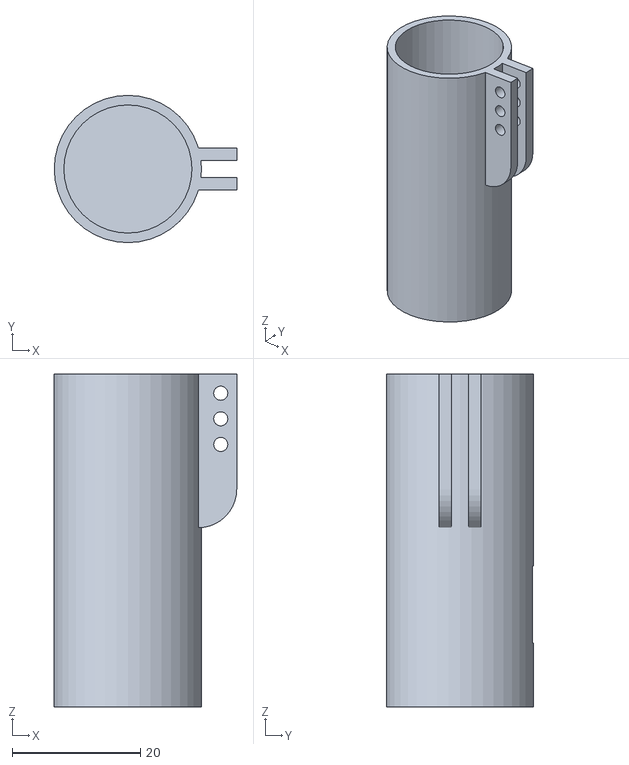
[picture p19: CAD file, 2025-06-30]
actuators/pull-solenoid/hitterLarge_new.stl
28.5 x 23.0 x 52.0

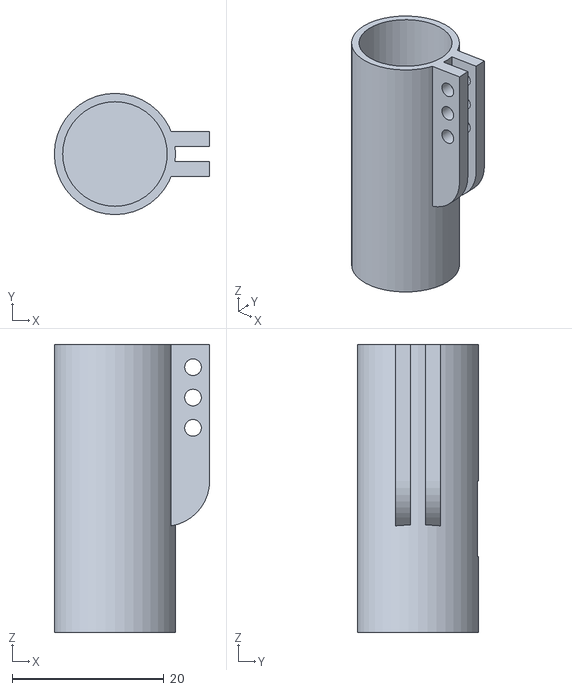
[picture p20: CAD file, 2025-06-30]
actuators/pull-solenoid/hitter_small.stl
20.5 x 16.0 x 38.0

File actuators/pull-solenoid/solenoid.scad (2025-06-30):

$fn=40;
hitter();
//plate();


module plate(){
difference(){
union(){cube([20,40,4.5]);
translate([10,0,0])cylinder(d=20,h=4.5);
    translate([0,13,4.5])cube([5,4,2.5]);
}
translate([10,0,0])cylinder(d=15,h=4.5);
translate([10,15,0])cylinder(d=5,h=4.5);
translate([10,30,0])cylinder(d=5.5,h=4.5);
translate([0.75,14.25,0])cube([3.5,1.5,8]);
}
}
module plate_small(){
difference(){
union(){cube([15,32.5,3]);
translate([7.5,0,0])cylinder(d=15,h=3);
    translate([0,13,3])cube([5,4,2.5]);
}
translate([7.5,0,0])cylinder(d=10,h=3);
translate([7.5,15,0])cylinder(d=5,h=3);
translate([7.5,25,0])cylinder(d=5.5,h=3);
translate([0.75,14.25,0])cube([3.5,1.5,6]);
}
}
module hitter(){
translate([0,-0,0]){difference(){
    cylinder(d=23,h=52);
    translate([0,0,10])cylinder(d=20,h=42.1);
    translate([-2,0,10])cube([4,20,12]);
}
translate([12.4,0,34]){
    
    difference(){
        union(){
            cylinder(d=3,h=18);
            translate([-1.5,-1.5,0])cube([1.5,3,18]);
        }
        cylinder(d=1,h=18);
    }

}
translate([-12.4,0,34]){
    
    difference(){
        union(){
            cylinder(d=3,h=18);
            translate([0,-1.5,0])cube([1.5,3,18]);
        }
        cylinder(d=1,h=18);
    }

}

}
}

module hitter_small(){
translate([0,-20,0]){difference(){
    cylinder(d=15,h=38);
    translate([0,0,10])cylinder(d=13.3,h=28.1);
    translate([-1.5,0,10])cube([3,10,10]);
}
translate([8.2,0,20]){
    
    difference(){
        union(){
            cylinder(d=3,h=18);
            translate([-1.5,-1.5,0])cube([1.5,3,18]);
        }
        cylinder(d=1,h=18);
    }

}
translate([-8.2,0,20]){
    
    difference(){
        union(){
            cylinder(d=3,h=18);
            translate([0,-1.5,0])cube([1.5,3,18]);
        }
        cylinder(d=1,h=18);
    }

}

}
}

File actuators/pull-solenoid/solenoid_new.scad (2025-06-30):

$fn=40;
//hitter();
//mirror()plate();
//mirror()plate_small();
hitter_small();
//link();
//link_small();

module link(){ difference(){
    union(){
cube([5,14.5,2]);
        translate([5,4,0])cube([5,10,2]);
translate([2.5,0,0])cylinder(d=5,h=2);
        translate([2.5,14.5,0])cylinder(d=5,h=2);
translate([2.5,12,0])cube([32.5,5,2]);
translate([35,14.5,0])cylinder(d=5,h=2);

    }
translate([2.5,0,0])cylinder(d=1.6,h=2);
translate([35,14.5,0])cylinder(d=1.6,h=2); 
 translate([1,8-1.5,0])cube([1.8,3.2,4]);
 translate([4,8-1.5,0])cube([1.8,3.2,4]);  
 translate([7,8-1.5,0])cube([1.8,3.2,4]);     
}}

module link_small(){ difference(){
    union(){
cube([5,10,1.4]);
        translate([5,2.8,0])cube([5,8,1.4]);
translate([2.5,0,0])cylinder(d=5,h=1.4);
        translate([2.5,10,0])cylinder(d=5,h=1.4);
translate([2.5,7.5,0])cube([28.5,5,1.4]);
translate([31,10,0])cylinder(d=5,h=1.4);

    }
translate([2.5,0,0])cylinder(d=1.6,h=2);
translate([31,10,0])cylinder(d=1.6,h=2); 
 translate([1,5.5-1.5,0])cube([1.8,3.2,4]);
 translate([4,5.5-1.5,0])cube([1.8,3.2,4]);  
 translate([7,5.5-1.5,0])cube([1.8,3.2,4]);     
}}
module plate(){
difference(){
union(){cube([20,40,4.5]);
translate([10,0,0])cylinder(d=20,h=4.5);
    translate([10,40,0])cylinder(d=20,h=4.5);
    translate([25,15,0])cylinder(d=20,h=4.5);
    translate([20,5,0])cube([5,20,4.5]);
    translate([0,13,4.5])cube([5,4,2.5]);
}
translate([10,0,0])cylinder(d=15,h=4.5);
translate([14,15,0])cylinder(d=4,h=4.5);
translate([10,40,0])cylinder(d=9.6,h=4.5);
 translate([25,15,0])cylinder(d=11.2,h=4.5);
translate([0.75,14.25,0])cube([3.5,1.5,8]);
}
}
module plate_small(){
difference(){
union(){cube([15,35,3]);
translate([7.5,0,0])cylinder(d=15,h=3);
    translate([7.5,35,0])cylinder(d=15,h=3);
    translate([20,15,0])cylinder(d=15,h=3);
    translate([15,7.5,0])cube([5,15,3]);
    translate([0,13,3])cube([5,4,2.5]);
}
translate([7.5,0,0])cylinder(d=10,h=3);
translate([10,15,0])cylinder(d=4,h=4.5);
translate([7.5,35,0])cylinder(d=9.6,h=4.5);
 translate([20,15,0])cylinder(d=11.2,h=4.5);
translate([1,14.25,0])cube([3,1.4,8]);
}
}
module hitter() {
  translate([0, -0, 0]) {
    difference() {
      union() {
        cylinder(d = 23, h = 52);
        translate([11, 0, 34]) {
          difference() {
            union() {
              translate([0, -3.3, 0])cube([6, 2, 18]);
              translate([0, 1.3, 0])cube([6, 2, 18]);
              translate([0, 3.3, 0])rotate([90, 0, 0])cylinder(d = 12, h = 2);
              translate([0, -1.3, 0])rotate([90, 0, 0])cylinder(d = 12, h = 2);
            }
            translate([3.5, 10, 15])rotate([90, 0, 0])cylinder(d = 2.2, h = 18);
            translate([3.5, 10, 11])rotate([90, 0, 0])cylinder(d = 2.2, h = 18);
            translate([3.5, 10, 7])rotate([90, 0, 0])cylinder(d = 2.2, h = 18);
          }
        }
      }
      translate([0, 0, 10])cylinder(d = 20, h = 42.1);
      translate([-2, 0, 10])cube([4, 20, 12]);
    }
  }
}

module hitter_small() {
  translate([0, -20, 0]) {
    difference() {
        union() {
      cylinder(d = 16, h = 38);
                translate([6.5, 0, 20]) {
          difference() {
            union() {
              translate([0, -3, 0])cube([6, 2, 18]);
              translate([0, 1, 0])cube([6, 2, 18]);
              translate([0, 3, 0])rotate([90, 0, 0])cylinder(d = 12, h = 2);
              translate([0, -1, 0])rotate([90, 0, 0])cylinder(d = 12, h = 2);
            }
            translate([3.8, 10, 15])rotate([90, 0, 0])cylinder(d = 2.2, h = 18);
            translate([3.8, 10, 11])rotate([90, 0, 0])cylinder(d = 2.2, h = 18);
            translate([3.8, 10, 7])rotate([90, 0, 0])cylinder(d = 2.2, h = 18);
          }
        }    
            
        }
      translate([0, 0, 10])cylinder(d = 13.8, h = 28.1);
      translate([-1.5, 0, 10])cube([3, 10, 10]);
    }
  }
}

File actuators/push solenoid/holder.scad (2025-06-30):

$fn=40;


difference(){
    hull(){
        cylinder(d=20,h=5);
        translate([0,18,0])cylinder(d=20,h=5);
        translate([0,-18,0])cylinder(d=10,h=5);
        translate([0,-28,0])cylinder(d=10,h=5);
    }
    cylinder(d=14.3,h=6);
    translate([0,18,0])cylinder(d=16,h=6);
            translate([0,-18,0])cylinder(d=4.8,h=6);
        translate([0,-28,0])cylinder(d=4.8,h=6);
}

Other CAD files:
actuators/pull-solenoid/plateLarge.stl
actuators/pull-solenoid/plate_small.stl
actuators/push solenoid/tapperdaiper.scad
atmegaDimmer/box/dimmerbox.scad
microRS485-MIDI/box/micromidirs485.scad

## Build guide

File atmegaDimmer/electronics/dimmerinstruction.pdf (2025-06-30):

Edwin Dertien - V1.0 - October 2021

# 8 channel RS485 control card

assembly manual

# step 1: IC sockets

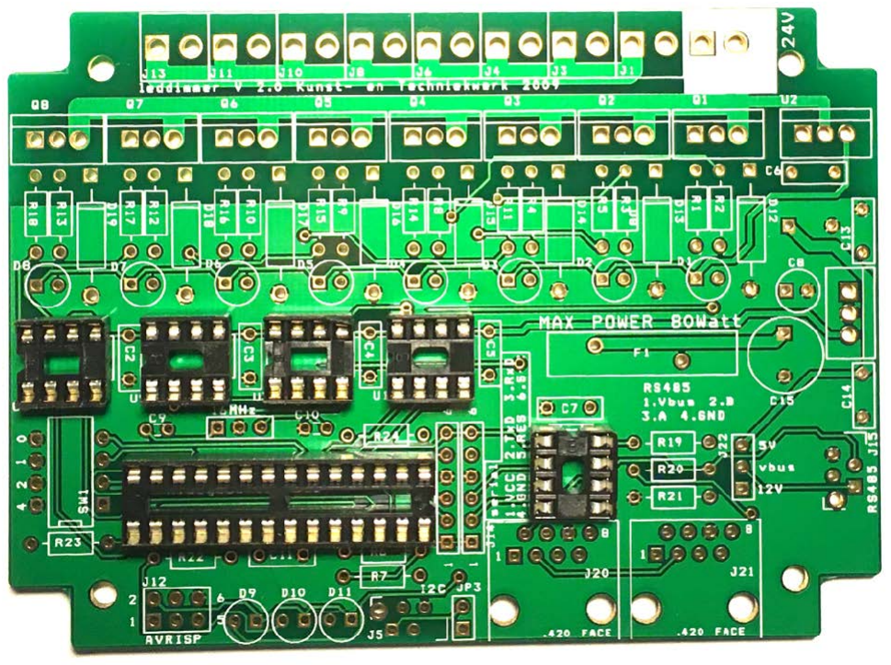
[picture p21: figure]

- 5 x 8 pin, 1 x 28 pin
- watch orientation

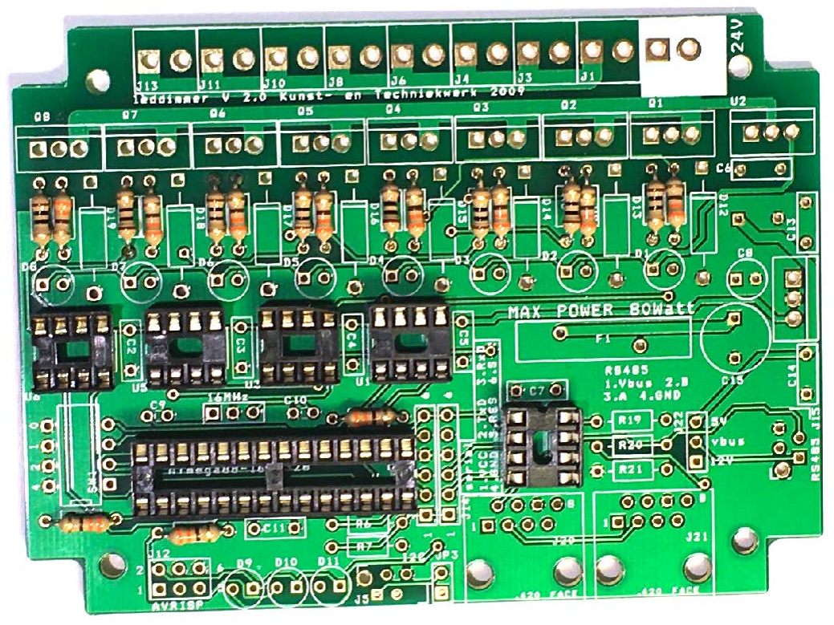
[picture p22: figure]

# step 2: resistors

- 8 + 3 x 330R (orange,
orange brown)
- 8 x 10R (brown, black,
black)

# step 3: xtal and cap

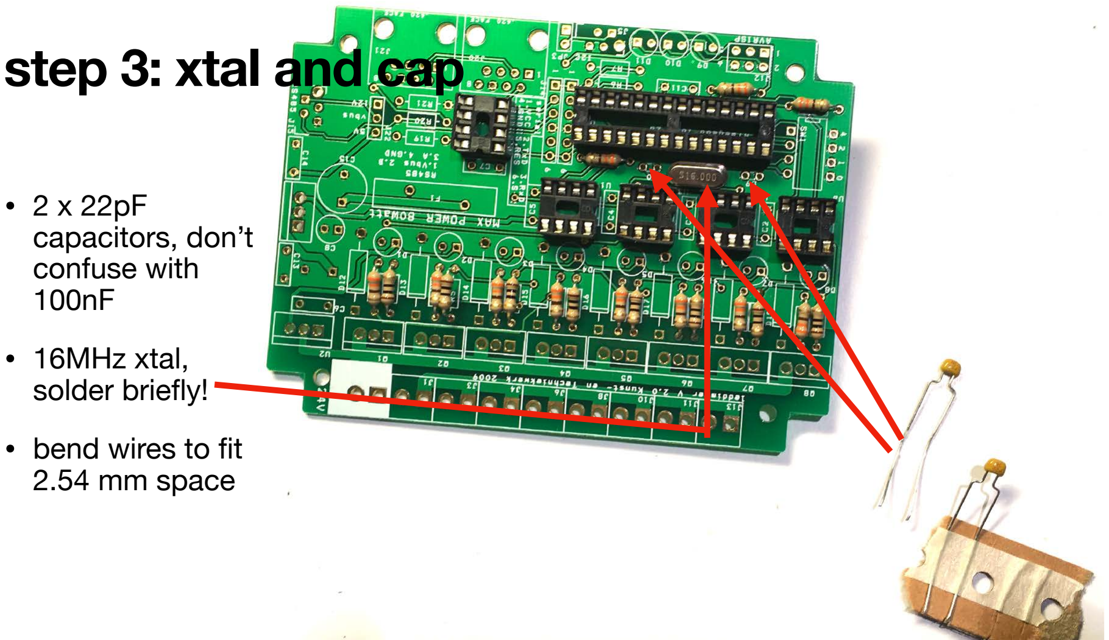
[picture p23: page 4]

- 2 x 22pF
capacitors, don’t
confuse with
100nF
- 16MHz xtal,
solder briefly!
- bend wires to fit
2.54 mm space

# step 4: diodes

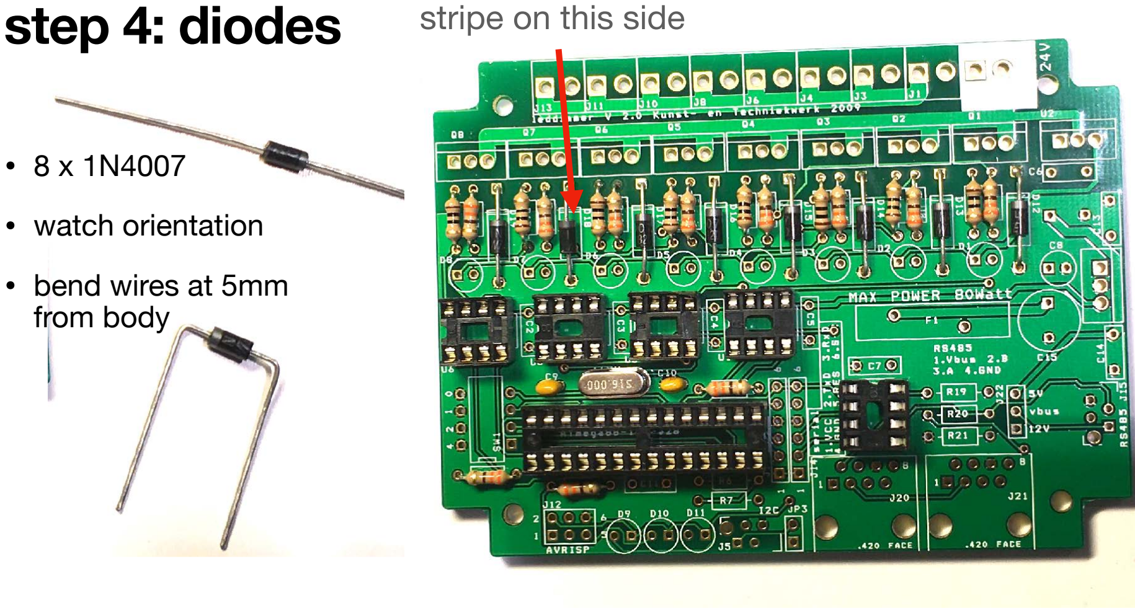
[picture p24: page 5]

- 8 x 1N4007
- watch orientation
- bend wires at 5mm
from body

stripe on this side

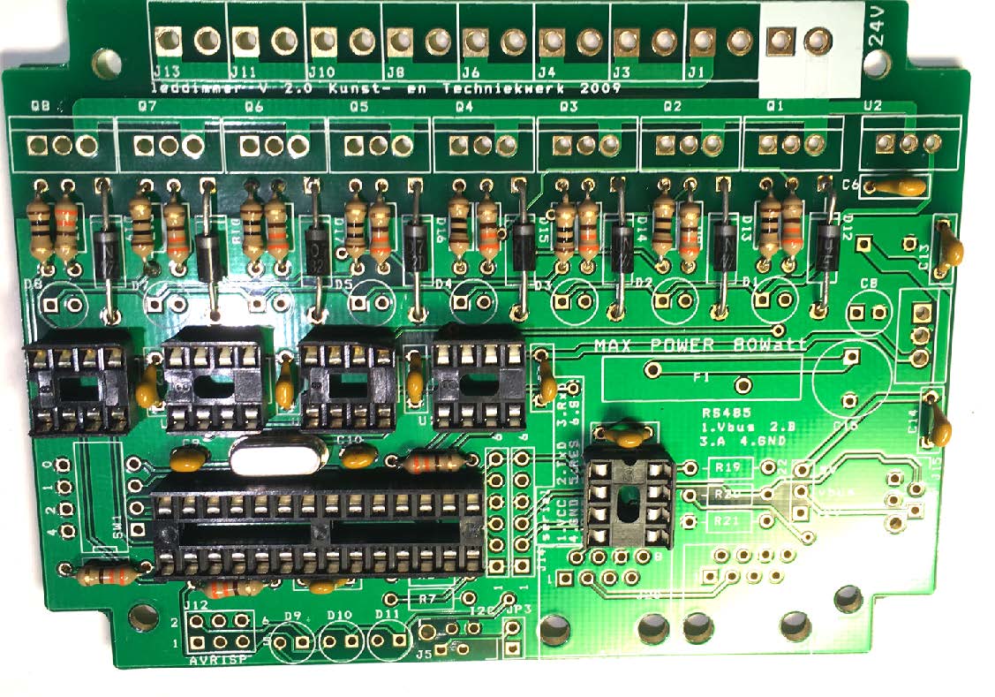
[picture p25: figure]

# step 5, 100n cap

- 9 x 100 nF
capacitor
- 6 x next to IC
socket, 3 x in power
supply section

# step 6: connector

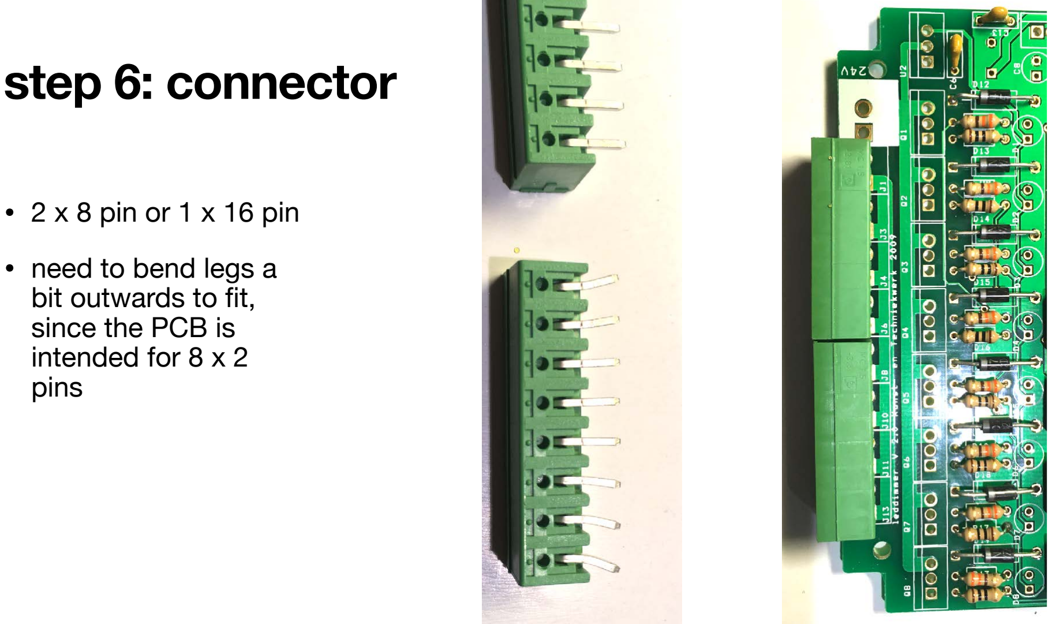
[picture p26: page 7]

- 2 x 8 pin or 1 x 16 pin
- need to bend legs a
bit outwards to fit,
since the PCB is
intended for 8 x 2
pins

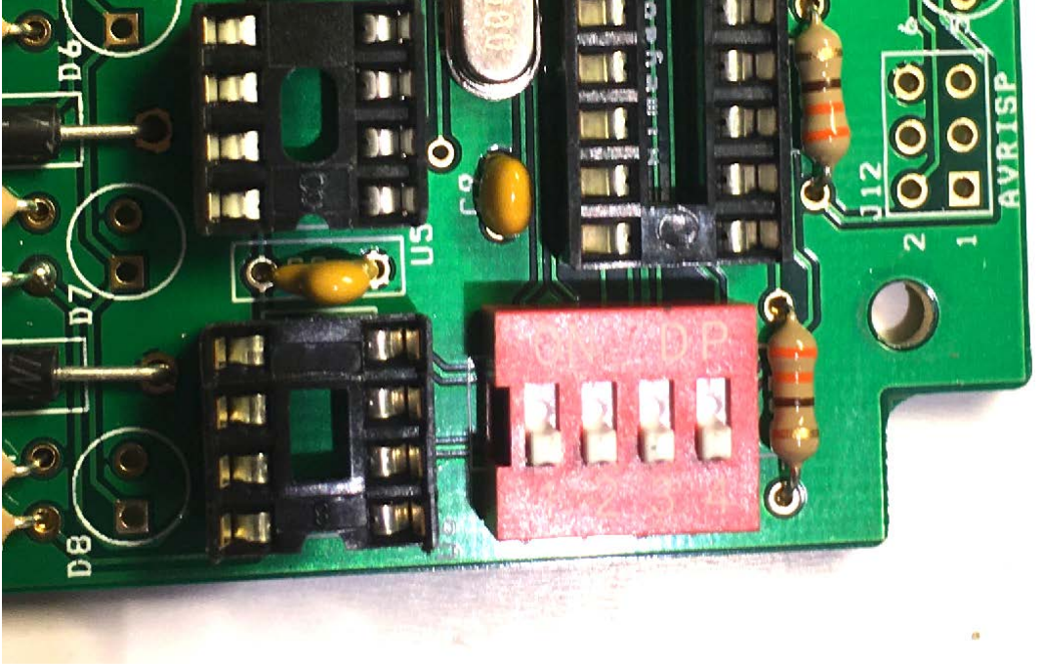
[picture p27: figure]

# step 7: dip switch

- check orientation, the
unit will work but
reversal is highly
confusing :)
- (so, the text should be
legible from the side)

# step 8a

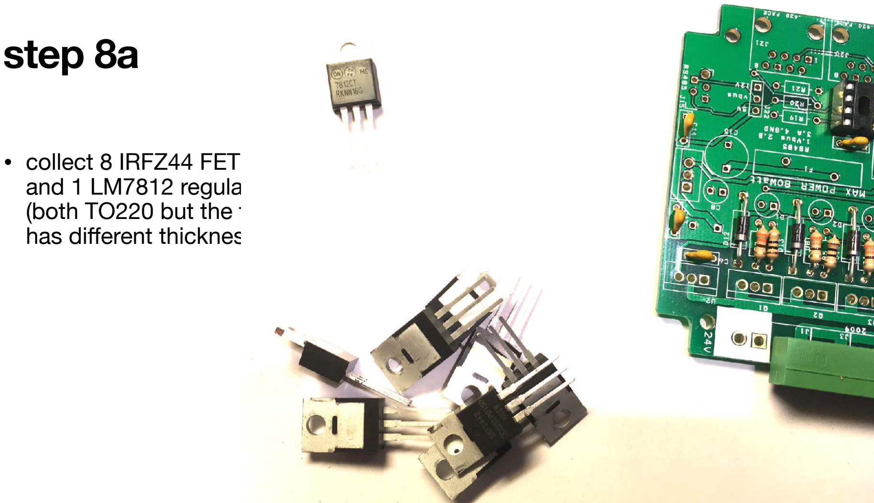
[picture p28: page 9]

- collect 8 IRFZ44 FET
and 1 LM7812 regulator
(both TO220 but the tab
has different thickness)

# step 8b

- mount 8 FETs, legs

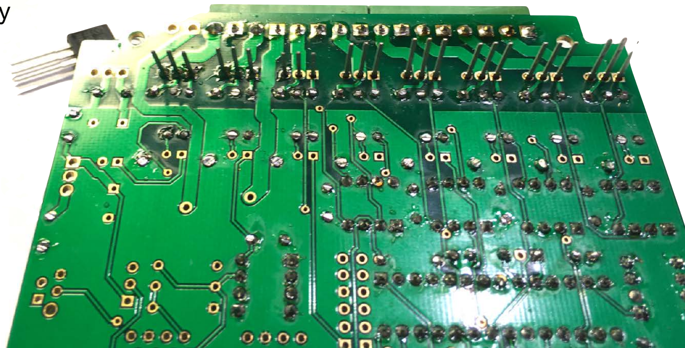
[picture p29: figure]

can get in all the way
(mount flush at PCB
side)

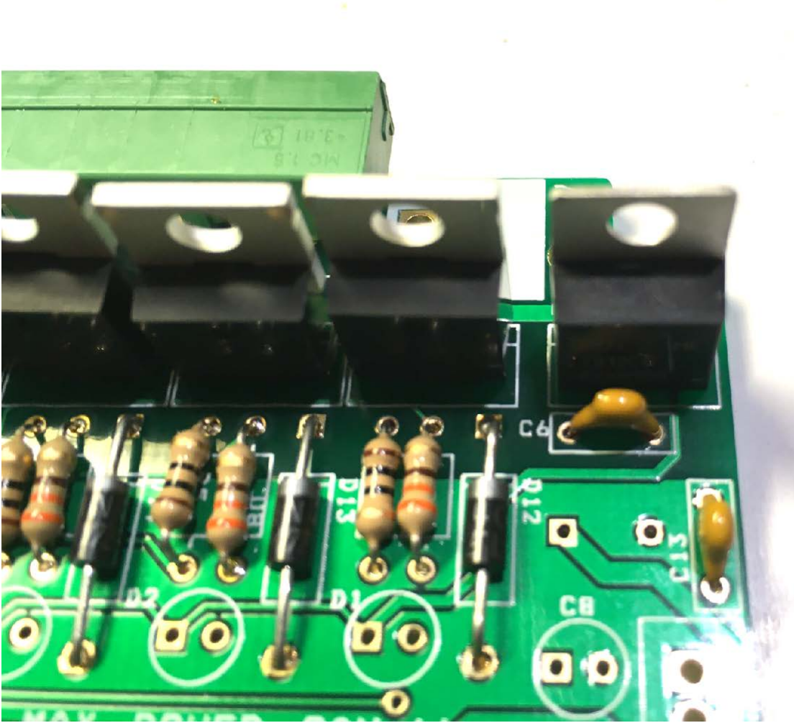
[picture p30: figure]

# step 9: LM7812

- mount the linear regulator (LM7812)

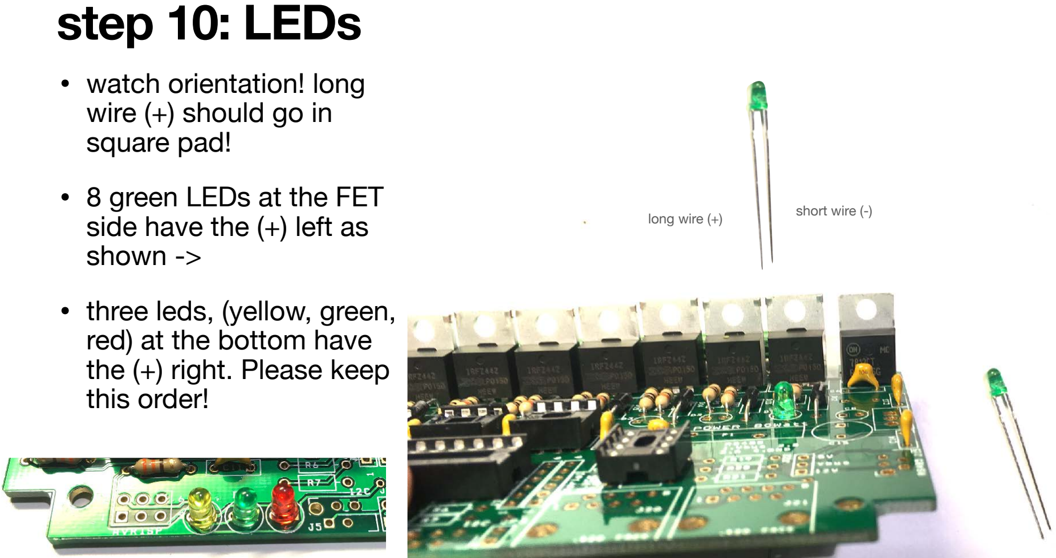
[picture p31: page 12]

step 10: LEDs • watch orientation! long

wire (+) should go in
square pad!
- 8 green LEDs at the FET
side have the (+) left as
shown ->
- three leds, (yellow, green, red) at the bottom have
the (+) right. Please keep this order!
long wire (+) | short wire (-)

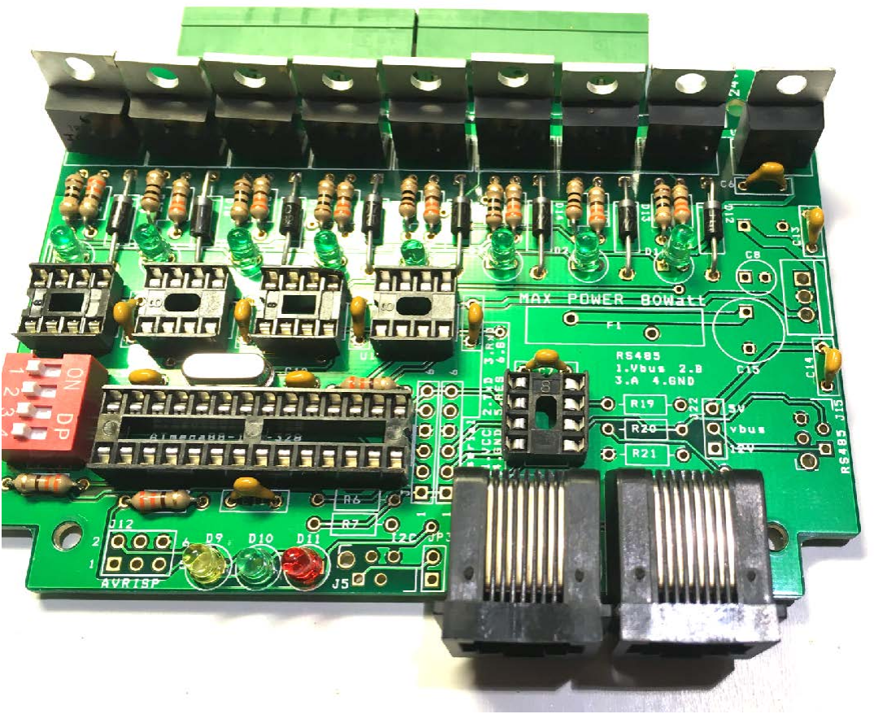
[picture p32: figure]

# step 11: RJ45

- Two RJ 45 sockets
- plastic strip on side of ONE of the sockets need to be taken off (knife, pliers) in order to fit

# step 12 regulator

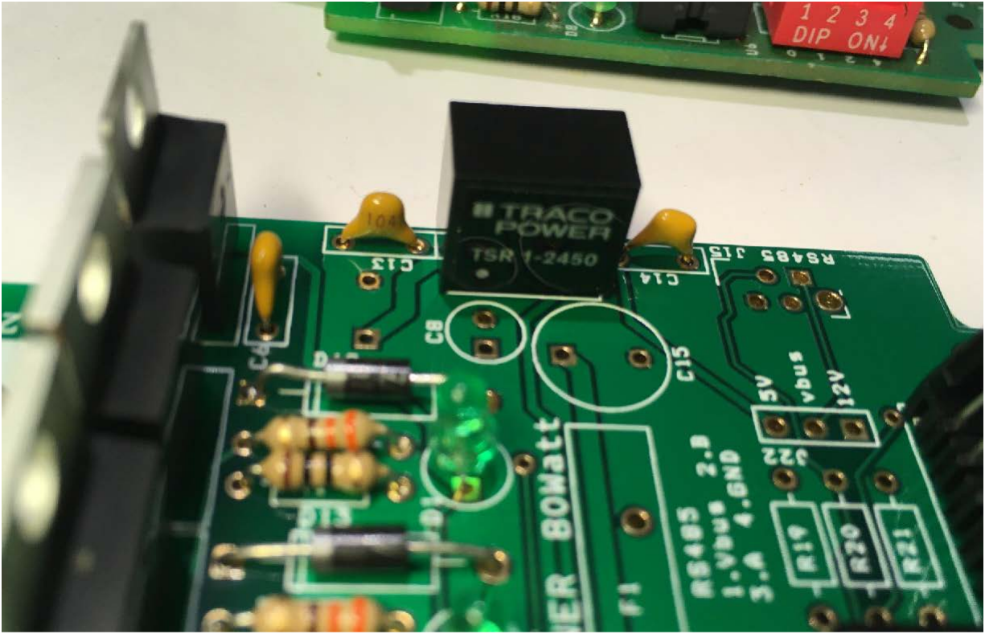
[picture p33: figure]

- Traco Power TSR
1-2450 regulator
- sloppy pin fit: mount
as much on the PCB
as possible

# step 13 elcos

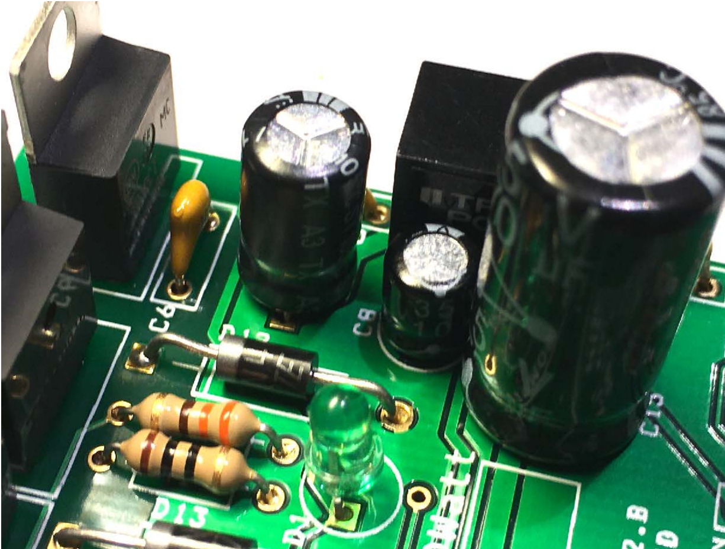
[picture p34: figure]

- mount three elco’s
- watch polarisation: stripe on side is (-)
- (+) side should go in
square pad
- check sizes

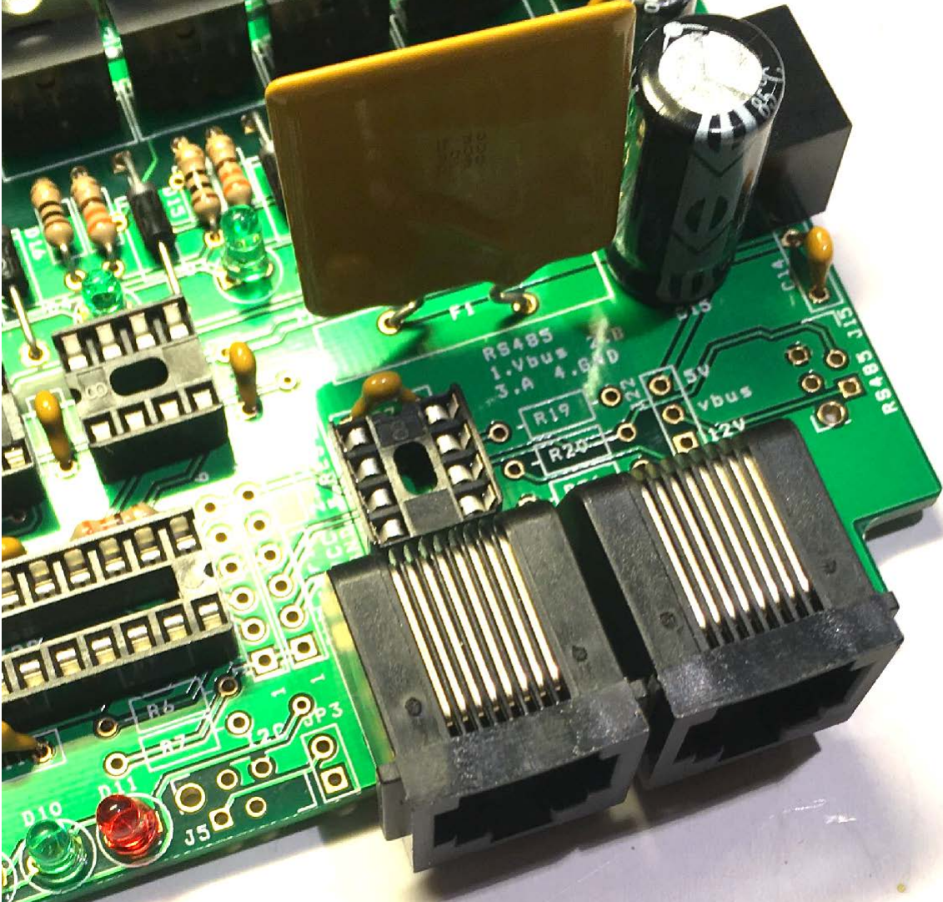
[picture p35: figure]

# step 14: fuse

- mount the fuse

# step 15: pin headers

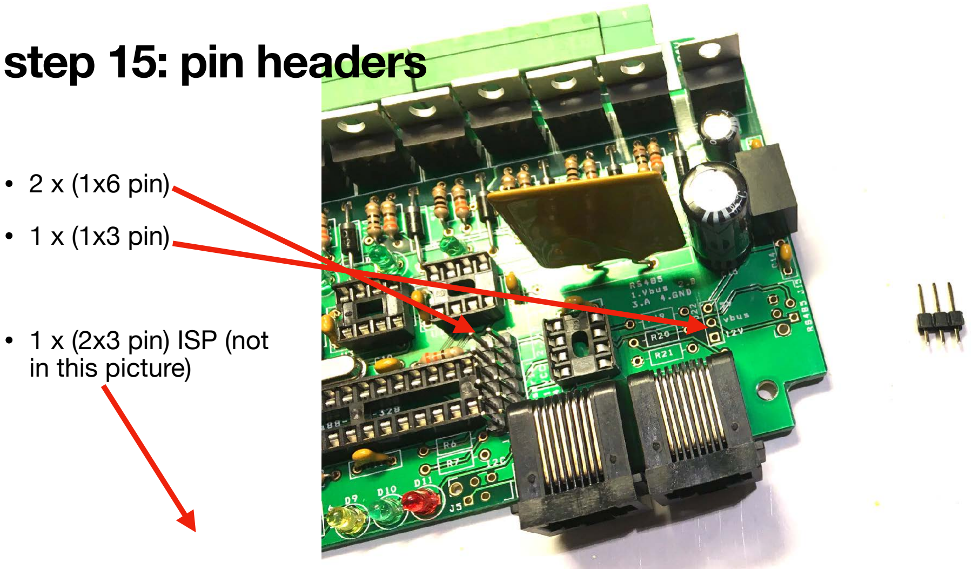
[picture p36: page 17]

- 2 x (1x6 pin)
- 1 x (1x3 pin)
- 1 x (2x3 pin) ISP (not
in this picture)

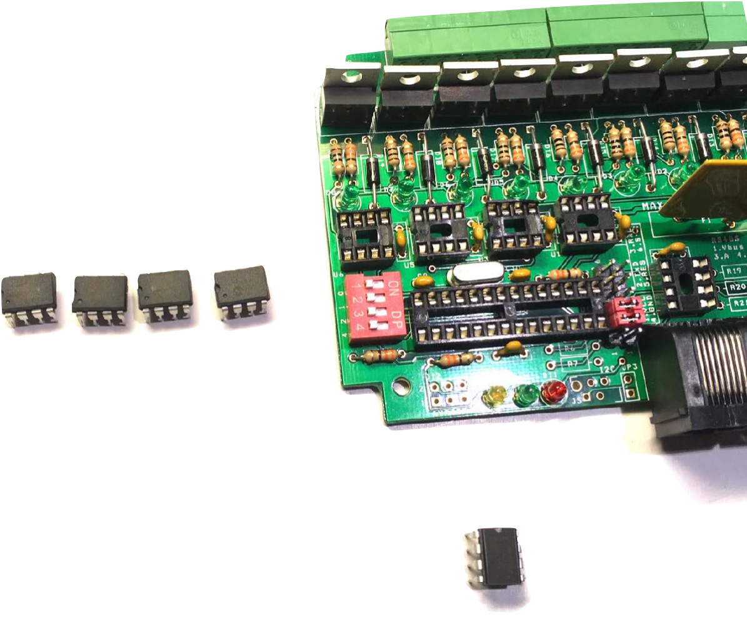
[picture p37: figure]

# step 16 IC’s

- (check!) 4 x TC4423 (in a row)
- 1 x MAX485 (or sipex or
similar) next to the RJ45
sockets
- 1 x ATmega88
- carefully bend the legs a bit (on the side on table)
- check orientation!

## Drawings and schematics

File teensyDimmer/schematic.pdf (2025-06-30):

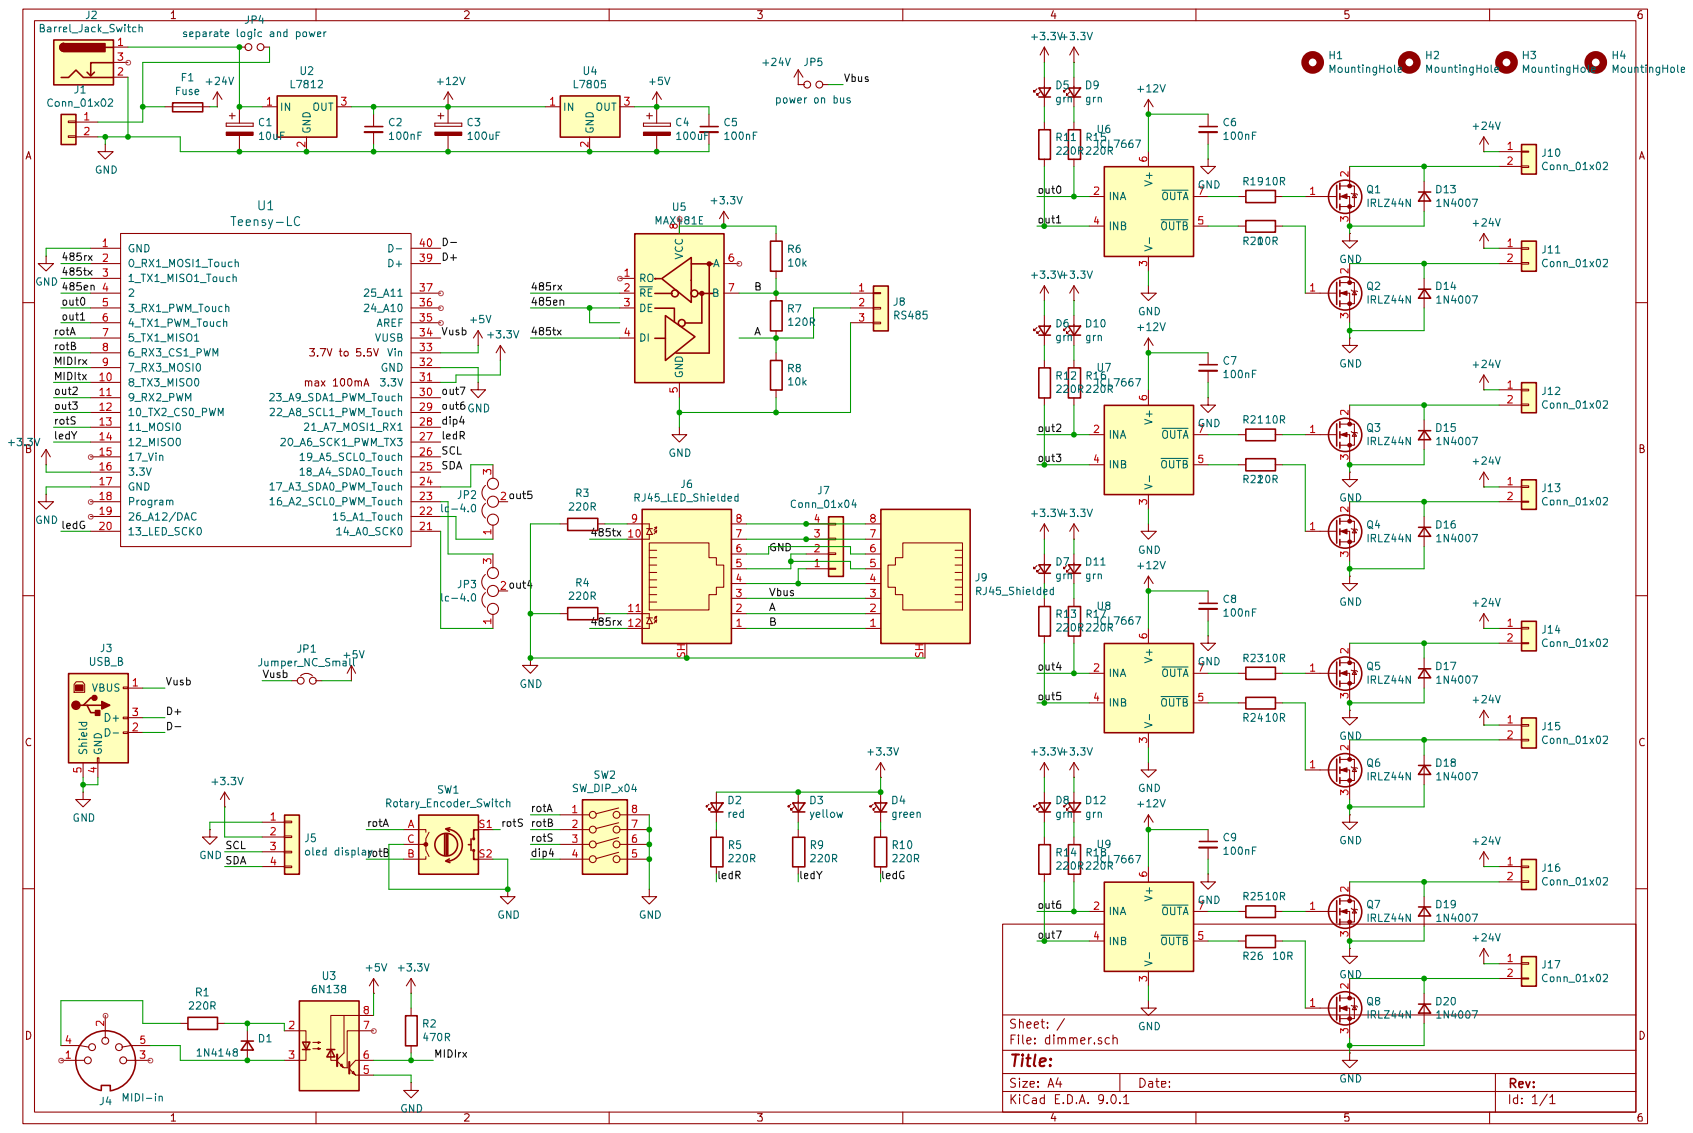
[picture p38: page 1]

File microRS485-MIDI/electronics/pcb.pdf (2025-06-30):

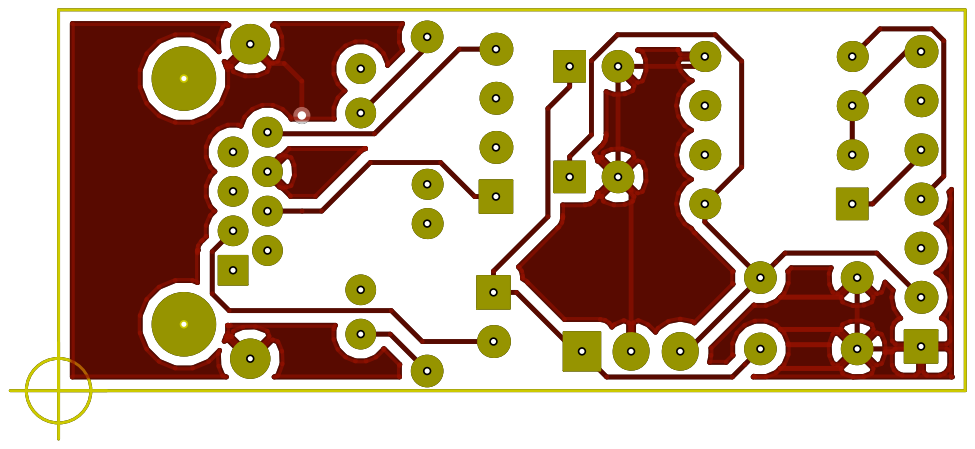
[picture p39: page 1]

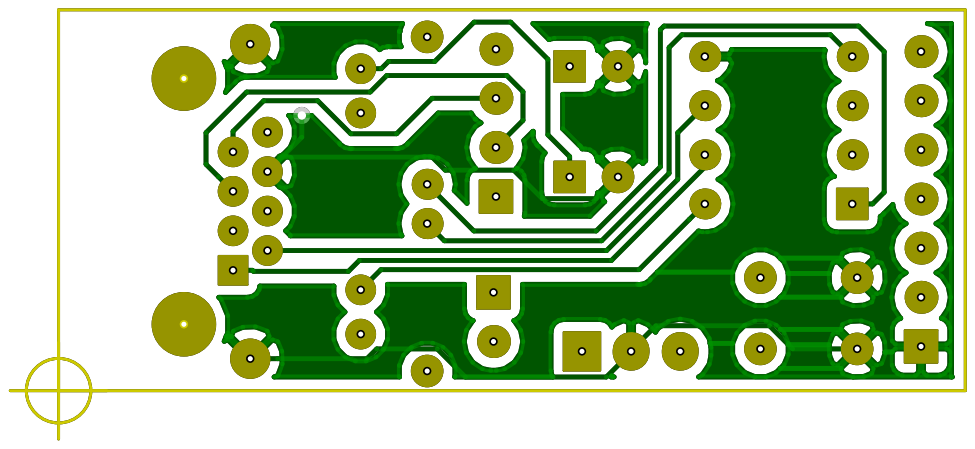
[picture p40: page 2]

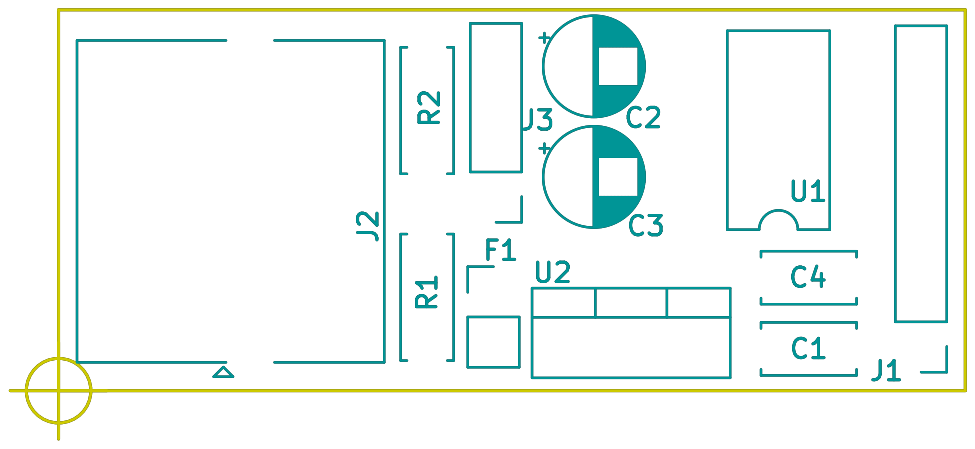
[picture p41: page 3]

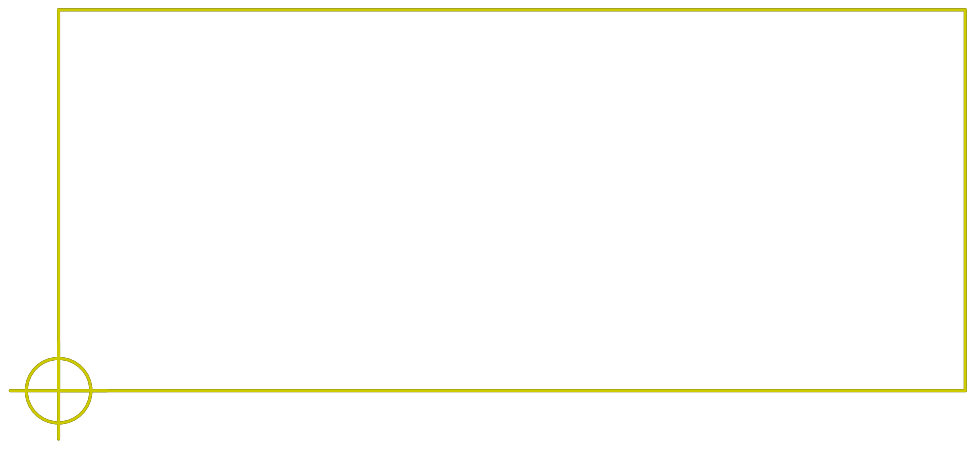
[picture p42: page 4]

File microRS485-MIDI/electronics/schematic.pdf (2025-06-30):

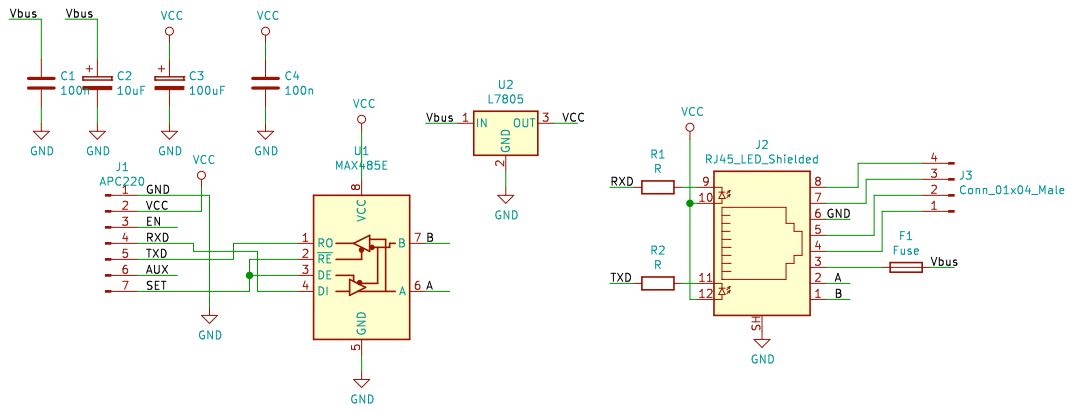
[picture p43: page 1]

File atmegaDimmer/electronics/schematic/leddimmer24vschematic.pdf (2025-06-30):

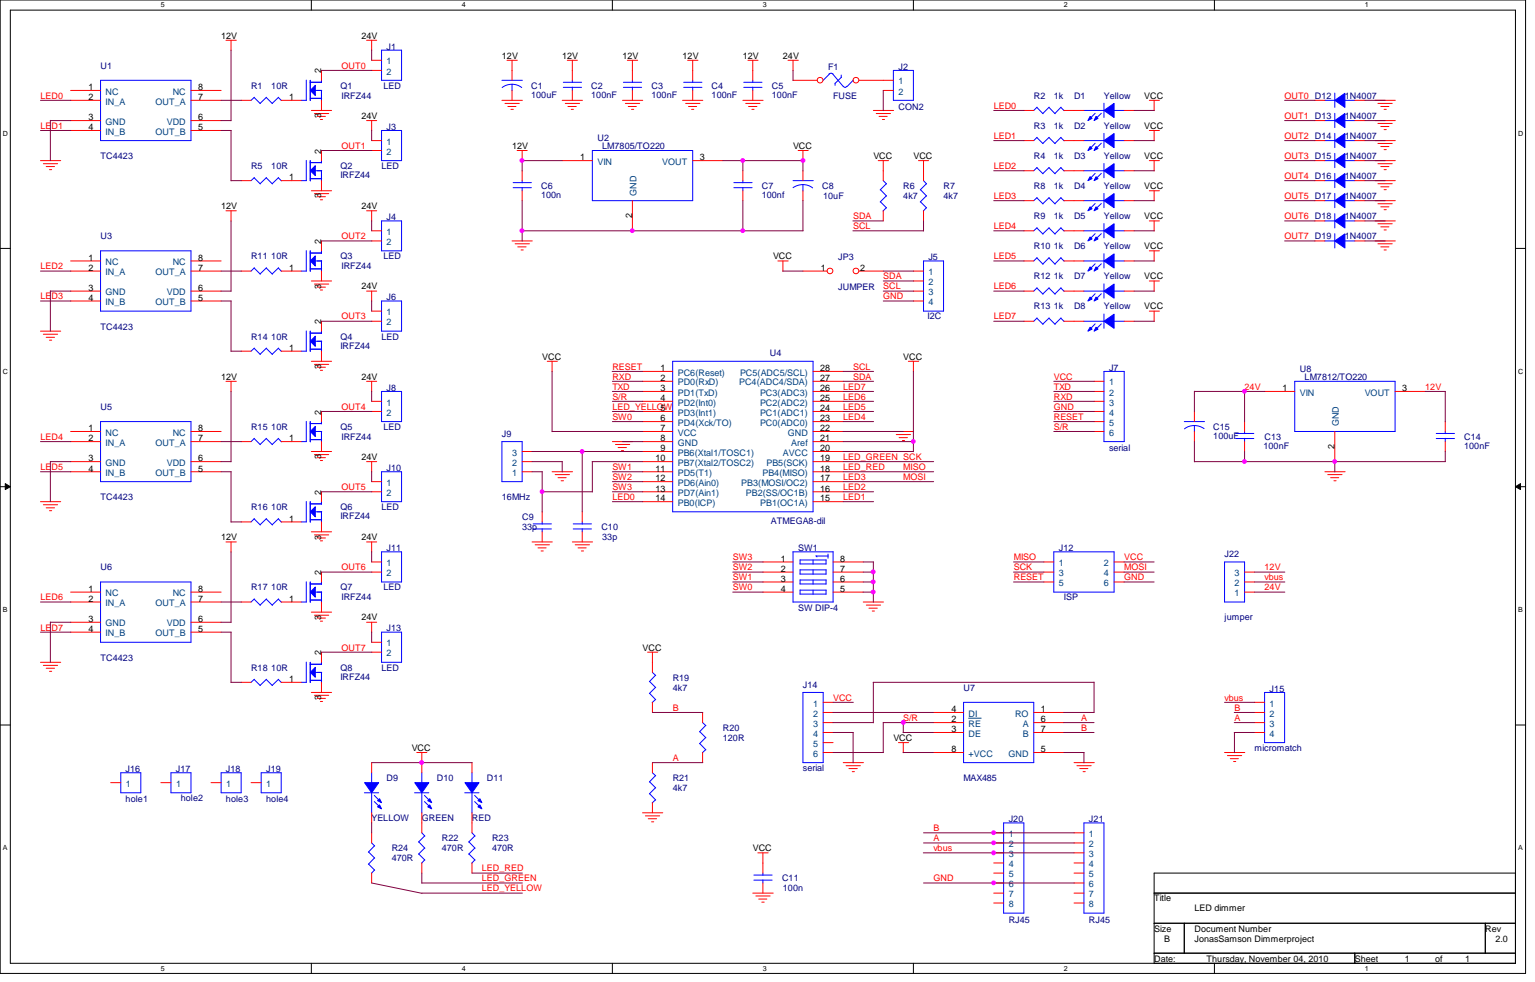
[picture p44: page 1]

Size B | Document Number JonasSamson Dimmerproject | Rev 2.0

Date: Thursday, November 04, 2010 | Sheet 1 of 1

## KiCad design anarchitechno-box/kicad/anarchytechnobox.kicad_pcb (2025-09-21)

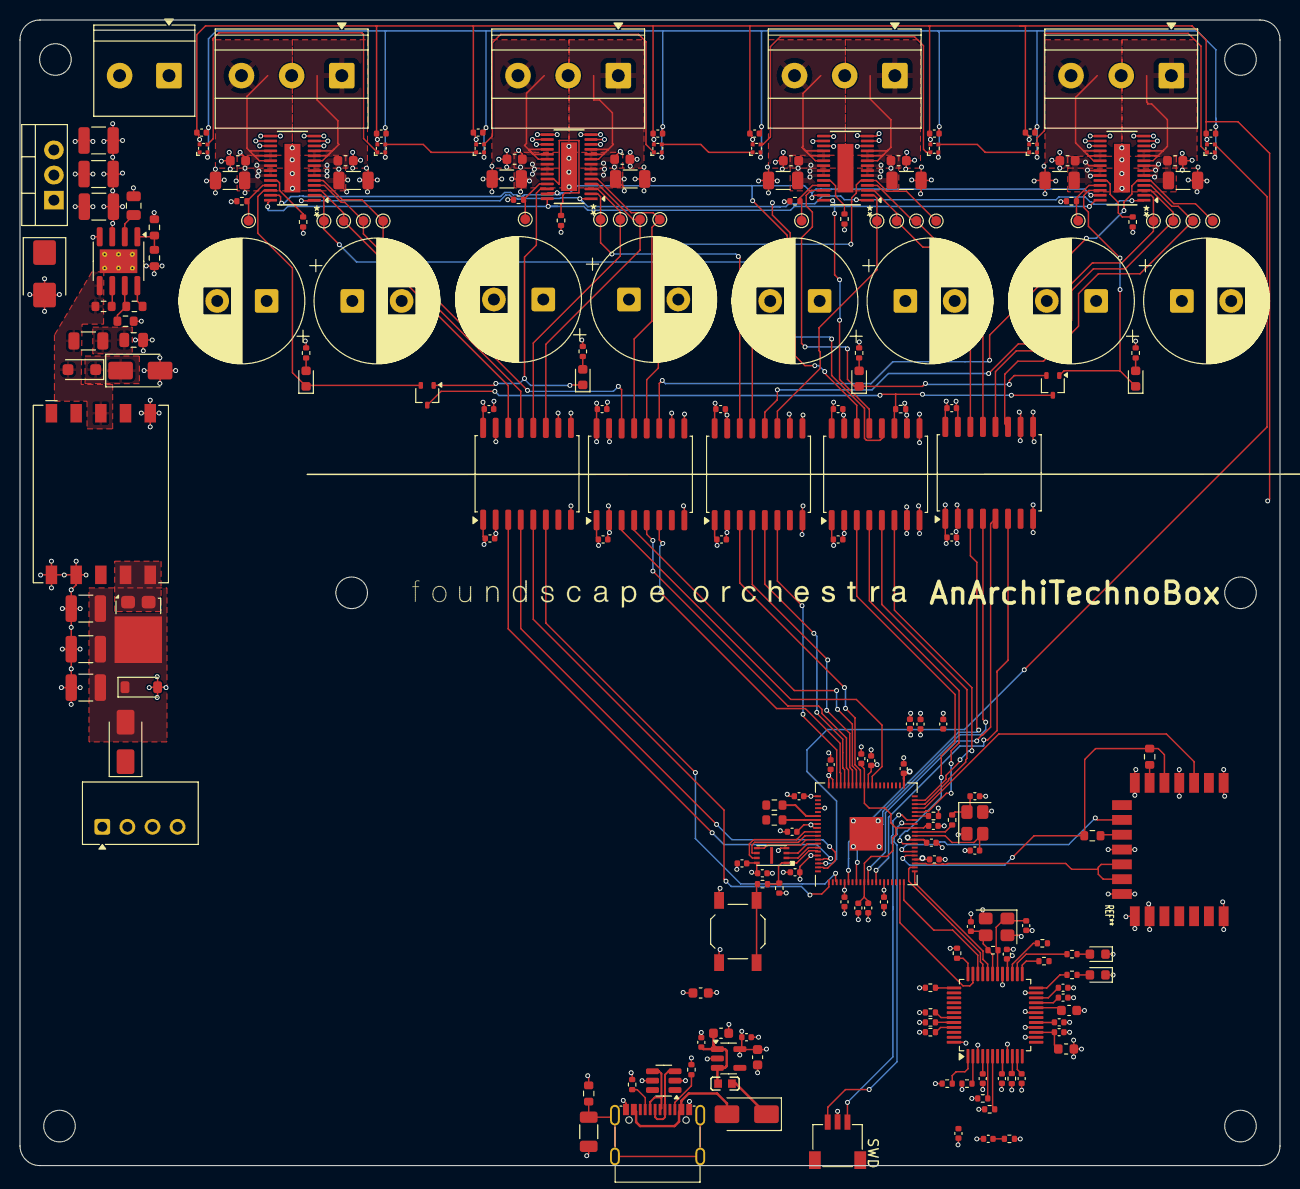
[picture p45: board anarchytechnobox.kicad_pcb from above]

Board: 4 copper layers, 127.6 x 116.0 mm, 216 parts (0 on the bottom side), 144 nets.

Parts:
C1, C2, C3, C4, C5, C7, C8, C11, C13, C14, C15, C16, C21, C22, C23, C27, C30, C31, C32, C33, C46, C47, C48, C49, C50, C51, C54, C55, C56, C58, C60, C61, C62, C86, C87, C88, C89, C90, C91: 100nF; C_0402_1005Metric
C6: 4.7u; C_0402_1005Metric
C9, C17: 100n; C_0402_1005Metric
C10, C18, C19: 1u; C_0402_1005Metric
C12, C20, C26: 10uF; C_0603_1608Metric
C24: 4.7n 100v; C_1206_3216Metric
C25: 0.1uF; C_0402_1005Metric
C28, C29: 27p; C_0402_1005Metric
C34, C35, C40, C41, C74, C75, C80, C81: 1uF 50V; C_0603_1608Metric
C36, C37, C42, C43, C76, C77, C82, C83: 10uF 50V; C_1206_3216Metric
C38, C39, C44, C45, C78, C79, C84, C85: 1000uF 50V; CP_Radial_D12.5mm_P5.00mm
C52, C53: 15p; C_0402_1005Metric
C57: 10nF; C_0402_1005Metric
C59: 4.7uF; C_0603_1608Metric
C63: 22n; C_0402_1005Metric
C64: 10n; C_0402_1005Metric
C65: 330uF 50V; C_1210_3225Metric
C66, C67: 10uF 50V; C_1210_3225Metric
C68: 1uF 25V; C_0805_2012Metric
C69: 220pF; C_0805_2012Metric
C70, C71, C72: 47uF 10V; C_1210_3225Metric
D1: SM6T24A; D_SMB
D2, D3, D18, D19, D20, D21, D22, D23: C5349953; XL-1010
D4, D5: BAT54AW; SOT-323_SC-70
D6, D7, D8, D9, D14, D15: RED; LED_0603_1608Metric
D10: SMAJ18A; D_SMA
D11: CMMSH1-100; D_SOD-123F
D12: V8PM10SHM3/I; TO-277A
D13: CMHZ5232B; D_SOD-123
D16, D17: SS34; D_SMA
FB1: BLM18PG121SN1D; L_0603_1608Metric
H1, H2, H3, H4, H5, H6: MountingHole; MountingHole_3.2mm_M3
J1: C2988369; USB-C C2988369
J2: Conn_01x03_Socket; SWD_TOP
J3, J4, J5, J6: Screw_Terminal_01x03; TerminalBlock_Phoenix_MKDS-1,5-3-5.08_1x03_P5.08mm_Horizont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
J7: Screw_Terminal_01x02; TerminalBlock_Phoenix_PT-1,5-2-5.0-H_1x02_P5.00mm_Horizontal
L1: BLM18PG121SN1D_C14709; L0603
Q1: 12mhz; Crystal_SMD_SeikoEpson_TSX3225-4Pin_3.2x2.5mm
R1: 470; R_0603_1608Metric
R2: 10k; R_0603_1608Metric
R3: 1M; R_0603_1608Metric
R4, R5: 5.1k; R_0402_1005Metric
R6, R10: 10k; R_0402_1005Metric
R7, R8: 27; R_0603_1608Metric
R9, R11: 1k; R_0402_1005Metric
R12, R15, R25, R26, R27, R28, R41, R44: 470R; R_0402_1005Metric
R13, R16, R42, R45: 0R; R_0402_1005Metric
R14, R17, R43, R46: TBD; R_0402_1005Metric
R18: 10K; R_0402_1005Metric
R19: 1MEG; R_0402_1005Metric
R20, R21, R22, R23, R24: 1K; R_0402_1005Metric
R29: 12.4k; R_0402_1005Metric
R30, R31, R33, R34: 49R9; R_0402_1005Metric
R32: 10R; R_0402_1005Metric
R35: 1MEG; R_0603_1608Metric
R36: 200K; R_0603_1608Metric
R37: 150K; R_0603_1608Metric
R38: 113K; R_0603_1608Metric
R39: 100R; R_1206_3216Metric
R40: 10K; R_0603_1608Metric
SW1: C318884; SW_SPST_TL3342
TP1, TP2, TP3, TP4, TP5, TP6, TP7, TP8, TP9, TP10, TP11, TP12, TP13, TP14, TP15, TP16, TP17, TP18, TP19, TP20: TestPoint; TestPoint_Pad_D1.0mm
U1: TME-0503S; Converter_DCDC_TRACO_TME_03xxS_05xxS_12xxS_Single_THT
U3: LM7812_TO220; TO-220-3_Vertical
U4: <value>; rpi_rmc20452t
U5: LP5907MFX-3.3; SOT-23-5
U7: C85364; SOT-23-6
U8: QFN-80_EP_10x10_Pitch0.4mm
U9, U10, U13, U14: ISO7740DWR; SOIC-16W_7.5x10.3mm_P1.27mm
U11, U12, U20, U21: DRV8243SQDGQRQ1; TI_HVSSOP-28
U15: ISO7742DWR; SOIC-16W_7.5x10.3mm_P1.27mm
U16: W5500; LQFP-48_7x7mm_P0.5mm
U18: ADPL54203ES8E#PBF; SOIC-8-1EP_3.9x4.9mm_P1.27mm_EP2.41x3.81mm_ThermalVias
U19: 750311564; T_Wurth_WE-FB-EP13_16.36
U$1: C2843335 W25Q16JVUXIQ; USON-8-EP(2x3)
Y1: 25MHz; Crystal_SMD_3225-4Pin_3.2x2.5mm

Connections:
+1V1: C18.2, C19.1, C21.1, C22.2, C23.1, U8.10 (DVDD), U8.32 (DVDD), U8.51 (DVDD)
+3.3VA: C55.1, C56.1, C58.1, C60.1, C61.1, C62.1, FB1.2, U16.4 (AVDD), U16.8 (AVDD), U16.11 (AVDD), U16.15 (AVDD), U16.17 (AVDD), U16.21 (AVDD)
+3.3VP: C31.1, C33.1, C49.1, C50.1, C51.1, R12.1, R13.1, R15.1, R16.1, R18.1, R41.1, R42.1, R44.1, R45.1, U9.10 (EN2), U9.16 (VCC2), U10.10 (EN2), U10.16 (VCC2), U13.10 (EN2), U13.16 (VCC2), U14.10 (EN2), U14.16 (VCC2), U15.10 (EN2), U15.16 (VCC2)
+3V3: C1.2, C2.2, C3.2, C4.2, C5.2, C6.1, C7.2, C8.2, C10.2, C11.2, C13.2, C14.2, C15.2, C16.2, C17.2, C20.1, C25.1, C26.1, C27.2, C30.1, C32.1, C46.1, C47.1, C48.1, C54.1, C86.2, C87.2, C88.2, C89.2, C90.2, C91.2, D2.2 (VDD), D3.2 (VDD), D18.2 (VDD), D19.2 (VDD), D20.2 (VDD), D21.2 (VDD), D22.2 (VDD), D23.2 (VDD), FB1.1, R6.2, R10.1, R20.1, R21.1, R22.1, R23.2, R24.2, R30.1, R31.1, R32.1, R33.1, R34.1, U4.14 (VDDIO), U4.16 (VIN), U5.5 (OUT), U7.5 (REF), U8.5 (IOVDD), U8.15 (IOVDD), U8.24 (IOVDD), U8.29 (IOVDD), U8.41 (IOVDD), U8.50 (IOVDD), U8.59 (ADC_IOVDD), U8.60 (IOVDD), U8.61 (VREG_AVDD), U8.64 (VREG_VIN), U8.68 (USB_OTP_VDD), U8.69 (QSPI_IOVDD), U8.76 (IOVDD), U9.1 (VCC1), U10.1 (VCC1), U13.1 (VCC1), U14.1 (VCC1), U15.1 (VCC1), U15.7 (EN1), U16.28 (VDD), U$1.8 (VCC)
+5V: D16.1 (K), D17.1 (K), L1.1, U1.2 (+Vin)
+24V: D1.1 (A1), U3.1 (VI)
+VDC: C34.1, C35.1, C36.1, C37.1, C38.1, C39.1, C40.1, C41.1, C42.1, C43.1, C44.1, C45.1, C65.1 (+), C66.1 (+), C67.1 (+), C69.1 (+), C74.1, C75.1, C76.1, C77.1, C78.1, C79.1, C80.1, C81.1, C82.1, C83.1, C84.1, C85.1, D10.2 (A), J7.1, R35.2 (-), U11.6 (VM), U11.7 (VM), U11.8 (VM), U11.21 (VM), U11.22 (VM), U11.23 (VM), U12.6 (VM), U12.7 (VM), U12.8 (VM), U12.21 (VM), U12.22 (VM), U12.23 (VM), U18.3 (VIN), U19.5 (N1_2), U20.6 (VM), U20.7 (VM), U20.8 (VM), U20.21 (VM), U20.22 (VM), U20.23 (VM), U21.6 (VM), U21.7 (VM), U21.8 (VM), U21.21 (VM), U21.22 (VM), U21.23 (VM)
/DCDC Flyback/PRE_5V: C70.1 (+), C71.1 (+), C72.1 (+), D12.3 (K), D13.1 (K), D17.2 (A)
/DCDC Flyback/PRE_PRE_5V: D12.1 (A), D12.2 (A), U19.6 (N2_1), U19.7 (N2_1)
/DCDC Flyback/VDC_CAPRES: C69.2 (-), R39.1 (+)
/DCDC Flyback/VDC_DIODES: D10.1 (K), D11.1 (K)
/DCDC Flyback/VDC_SW: D11.2 (A), R37.2 (-), R39.2 (-), U18.5 (SW), U19.3 (N1_1)
/Ethernet/ETH_RX_M: R34.2, U16.5 (RXN)
/Ethernet/ETH_RX_P: R33.2, U16.6 (RXP)
/Ethernet/ETH_TX_M: R31.2, U16.1 (TXN)
/Ethernet/ETH_TX_P: R30.2, U16.2 (TXP)
/Ethernet/SPI_CS: U8.21 (GPIO21), U16.32 (~SCS)
/Ethernet/SPI_INT: R23.1, U16.36 (~INT)
/Ethernet/SPI_MISO: U8.20 (GPIO20), U16.34 (MISO)
/Ethernet/SPI_MOSI: U8.19 (GPIO19), U16.35 (MOSI)
/Ethernet/SPI_RST: R24.1, U16.37 (~RST)
/Ethernet/SPI_SCK: U8.22 (GPIO22), U16.33 (SCLK)
/HB_1_OUT_A: J3.1, U20.9 (OUT1), U20.10 (OUT1), U20.11 (OUT1)
/HB_1_OUT_B: J3.3, U20.18 (OUT2), U20.19 (OUT2), U20.20 (OUT2)
/HB_1_OUT_C: J4.1, U21.9 (OUT1), U21.10 (OUT1), U21.11 (OUT1)
/HB_1_OUT_D: J4.3, U21.18 (OUT2), U21.19 (OUT2), U21.20 (OUT2)
/HB_2_OUT_A: J5.1, U11.9 (OUT1), U11.10 (OUT1), U11.11 (OUT1)
/HB_2_OUT_B: J5.3, U11.18 (OUT2), U11.19 (OUT2), U11.20 (OUT2)
/HB_2_OUT_C: J6.1, U12.9 (OUT1), U12.10 (OUT1), U12.11 (OUT1)
/HB_2_OUT_D: J6.3, U12.18 (OUT2), U12.19 (OUT2), U12.20 (OUT2)
/Isolators/MCU_CS1: U8.52 (GPIO41_ADC1), U14.3 (INA)
/Isolators/MCU_CS2: U8.54 (GPIO43_ADC3), U14.4 (INB)
/Isolators/MCU_CS3: U8.56 (GPIO45_ADC5), U14.5 (INC)
/Isolators/MCU_CS4: U8.58 (GPIO47_ADC7), U14.6 (IND)
/Isolators/MCU_DRV_nFAULT_COMMON: U8.39 (GPIO31), U15.6 (OUTD)
/Isolators/MCU_PWM_A_OFF: U8.49 (GPIO40_ADC0), U13.3 (INA)
/Isolators/MCU_PWM_B_OFF: U8.53 (GPIO42_ADC2), U13.4 (INB)
/Isolators/MCU_PWM_C_OFF: U8.55 (GPIO44_ADC4), U13.5 (INC)
/Isolators/MCU_PWM_D_OFF: U8.57 (GPIO46_ADC6), U13.6 (IND)
/Isolators/MCU_SPI_CLK: U8.28 (GPIO27), U15.3 (INA)
/Isolators/MCU_SPI_MISO: U8.38 (GPIO30), U15.5 (OUTC)
/Isolators/MCU_SPI_MOSI: U8.36 (GPIO28), U15.4 (INB)
/Isolators/PWR_DRV_nFAULT_COMMON: D4.3, D5.3, R18.2, U15.11 (IND)
/Isolators/PWR_PWM_A_OFF: TP19.1, U13.14 (OUTA), U21.5 (DRVOFF)
/Isolators/PWR_PWM_B_OFF: TP14.1, U13.13 (OUTB), U20.5 (DRVOFF)
/Isolators/PWR_PWM_C_OFF: TP9.1, U12.5 (DRVOFF), U13.12 (OUTC)
/Isolators/PWR_PWM_D_OFF: TP4.1, U11.5 (DRVOFF), U13.11 (OUTD)
/Isolators/PWR_SPI_CLK: U11.1 (SCLK), U12.1 (SCLK), U15.14 (OUTA), U20.1 (SCLK), U21.1 (SCLK)
/Isolators/PWR_SPI_CS1: TP15.1, U14.14 (OUTA), U20.2 (nSCS)
/Isolators/PWR_SPI_CS2: TP20.1, U14.13 (OUTB), U21.2 (nSCS)
/Isolators/PWR_SPI_CS3: TP5.1, U11.2 (nSCS), U14.12 (OUTC)
/Isolators/PWR_SPI_CS4: TP10.1, U12.2 (nSCS), U14.11 (OUTD)
/Isolators/PWR_SPI_MISO: U11.27 (SDO), U12.27 (SDO), U15.12 (INC), U20.27 (SDO), U21.27 (SDO)
/Isolators/PWR_SPI_MOSI: U11.28 (SDI), U12.28 (SDI), U15.13 (OUTB), U20.28 (SDI), U21.28 (SDI)
/LED_STRING: D2.4 (DI), U8.78 (GPIO1)
/RP2350BMCU/5V_filtered: C9.2, C12.1, L1.2, U5.1 (IN), U5.3 (EN)
/RP2350BMCU/BOOTSEL_BUT: R9.2, SW1.2
/RP2350BMCU/BREAKOUT_5V: D16.2 (A), J1.A4B9 (VBUS), J1.A9B4 (VBUS)
/RP2350BMCU/MEM_CLK: U8.71 (QSPI_SCLK), U$1.6 (CLK)
/RP2350BMCU/MEM_CS: R6.1, R9.1, U8.75 (QSPI_SS), U$1.1 (/CS)
/RP2350BMCU/MEM_IO0: U8.72 (QSPI_SD0), U$1.5 (DI)
/RP2350BMCU/MEM_IO1: U8.74 (QSPI_SD1), U$1.2 (DO)
/RP2350BMCU/MEM_IO2: U8.73 (QSPI_SD2), U$1.3 (IO2)
/RP2350BMCU/MEM_IO3: U8.70 (QSPI_SD3), U$1.7 (IO3)
/RP2350BMCU/PMW1_A: U8.79 (GPIO2), U9.4 (INB)
/RP2350BMCU/PWM0_A: U8.77 (GPIO0), U9.3 (INA)
/RP2350BMCU/PWM2_A: U8.1 (GPIO4), U9.5 (INC)
/RP2350BMCU/PWM3_A: U8.3 (GPIO6), U9.6 (IND)
/RP2350BMCU/PWM4_A: U8.6 (GPIO8), U10.3 (INA)
/RP2350BMCU/PWM5_A: U8.8 (GPIO10), U10.4 (INB)
/RP2350BMCU/PWM6_A: U8.11 (GPIO12), U10.5 (INC)
/RP2350BMCU/PWM7_A: U8.13 (GPIO14), U10.6 (IND)
/RP2350BMCU/RUN: R10.2, U8.35 (RUN)
/RP2350BMCU/SWCLK: J2.1, U8.33 (SWCLK)
/RP2350BMCU/SWDIO: J2.3, U8.34 (SWD)
/RP2350BMCU/USB_N: J1.A7 (DN1), J1.B7 (DN2), R8.1, U7.4 (IO3)
/RP2350BMCU/USB_P: J1.A6 (DP1), J1.B6 (DP2), R7.1, U7.3 (IO2)
/RP2350BMCU/USB_PRE_N: R8.2, U8.66 (USB_DN)
/RP2350BMCU/USB_PRE_P: R7.2, U8.67 (USB_DP)
/RP2350BMCU/WIFI_23: U4.12 (WL_ON), U4.13 (BT_ON), U8.23 (GPIO23)
/RP2350BMCU/WIFI_24: R1.2, R2.2, U4.5 (DI), U8.25 (GPIO24)
/RP2350BMCU/WIFI_25: U4.9 (CS), U8.26 (GPIO25)
/RP2350BMCU/WIFI_29: U4.3 (SCLK), U8.37 (GPIO29)
/TwoIsolatedFETs0/HBridge_A/DRV_ISENSE: R46.1, TP16.1, U21.25 (IPROPI)
/TwoIsolatedFETs0/HBridge_A/DRV_nFAULT: D4.2, D15.1 (K), U21.26 (nFAULT)
/TwoIsolatedFETs0/HBridge_B/DRV_ISENSE: R43.1, TP11.1, U20.25 (IPROPI)
/TwoIsolatedFETs0/HBridge_B/DRV_nFAULT: D4.1, D14.1 (K), U20.26 (nFAULT)
/TwoIsolatedFETs0/PWM_A_1: TP18.1, U9.13 (OUTB), U21.4 (EN/IN1)
/TwoIsolatedFETs0/PWM_A_2: TP17.1, U9.14 (OUTA), U21.3 (PH/IN2)
/TwoIsolatedFETs0/PWM_B_1: TP13.1, U9.11 (OUTD), U20.4 (EN/IN1)
/TwoIsolatedFETs0/PWM_B_2: TP12.1, U9.12 (OUTC), U20.3 (PH/IN2)
/TwoIsolatedFETs1/HBridge_A/DRV_ISENSE: R17.1, TP6.1, U12.25 (IPROPI)
/TwoIsolatedFETs1/HBridge_A/DRV_nFAULT: D5.2, D7.1 (K), U12.26 (nFAULT)
/TwoIsolatedFETs1/HBridge_B/DRV_ISENSE: R14.1, TP1.1, U11.25 (IPROPI)
/TwoIsolatedFETs1/HBridge_B/DRV_nFAULT: D5.1, D6.1 (K), U11.26 (nFAULT)
/TwoIsolatedFETs1/PWM_A_1: TP8.1, U10.13 (OUTB), U12.4 (EN/IN1)
/TwoIsolatedFETs1/PWM_A_2: TP7.1, U10.14 (OUTA), U12.3 (PH/IN2)
/TwoIsolatedFETs1/PWM_B_1: TP3.1, U10.11 (OUTD), U11.4 (EN/IN1)
/TwoIsolatedFETs1/PWM_B_2: TP2.1, U10.12 (OUTC), U11.3 (PH/IN2)
GND: C1.1, C2.1, C3.1, C4.1, C5.1, C6.2, C7.1, C8.1, C9.1, C10.1, C11.1, C12.2, C13.1, C14.1, C15.1, C16.1, C17.1, C18.1, C19.2, C20.2, C21.2, C22.1, C23.2, C24.1, C25.2, C26.2, C27.1, C28.2, C29.2, C30.2, C32.2, C46.2, C47.2, C48.2, C52.2, C53.2, C54.2, C55.2, C56.2, C57.2, C58.2, C59.2, C60.2, C61.2, C62.2, C63.1, C64.1, C70.2 (-), C71.2 (-), C72.2 (-), C86.1, C87.1, C88.1, C89.1, C90.1, C91.1, D2.3 (GND), D3.3 (GND), D8.1 (K), D9.1 (K), D13.2 (A), D18.3 (GND), D19.3 (GND), D20.3 (GND), D21.3 (GND), D22.3 (GND), D23.3 (GND), J1.A1B12 (GND), J1.A12B1 (GND), J2.2, Q1.2 (G2), Q1.4 (G1), R3.1, R4.2, R5.2, R29.2, SW1.1, U1.3 (-Vout), U4.1 (GND), U4.4 (GND), U4.7 (GND), U4.11 (GND), U4.15 (GND), U4.21 (GND), U5.2 (GND), U7.2 (GND), U8.81 (GND), U9.2 (GND1), U9.8 (GND1), U10.2 (GND1), U10.8 (GND1), U13.2 (GND1), U13.8 (GND1), U14.2 (GND1), U14.8 (GND1), U15.2 (GND1), U15.8 (GND1), U16.3 (AGND), U16.9 (AGND), U16.14 (AGND), U16.16 (AGND), U16.19 (AGND), U16.23 (RSVD), U16.29 (GND), U16.48 (AGND), U19.9 (N2_2), U19.10 (N2_2), U$1.4 (GND), Y1.2, Y1.4
GND2: C31.2, C33.2, C34.2, C35.2, C36.2, C37.2, C38.2, C39.2, C40.2, C41.2, C42.2, C43.2, C44.2, C45.2, C49.2, C50.2, C51.2, C65.2 (-), C66.2 (-), C67.2 (-), C68.2 (-), C74.2, C75.2, C76.2, C77.2, C78.2, C79.2, C80.2, C81.2, C82.2, C83.2, C84.2, C85.2, D1.2 (A2), J3.2, J4.2, J5.2, J6.2, J7.2, R14.2, R17.2, R36.1 (+), R40.2 (-), R43.2, R46.2, U1.1 (-Vin), U3.2 (GND), U9.9 (GND2), U9.15 (GND2), U10.9 (GND2), U10.15 (GND2), U11.12 (GND), U11.13 (GND), U11.14 (GND), U11.15 (GND), U11.16 (GND), U11.17 (GND), U11.EP (GND), U12.12 (GND), U12.13 (GND), U12.14 (GND), U12.15 (GND), U12.16 (GND), U12.17 (GND), U12.EP (GND), U13.9 (GND2), U13.15 (GND2), U14.9 (GND2), U14.15 (GND2), U15.9 (GND2), U15.15 (GND2), U18.4 (GND), U18.9 (GND), U20.12 (GND), U20.13 (GND), U20.14 (GND), U20.15 (GND), U20.16 (GND), U20.17 (GND), U20.EP (GND), U21.12 (GND), U21.13 (GND), U21.14 (GND), U21.15 (GND), U21.16 (GND), U21.17 (GND), U21.EP (GND)
unnamed: C24.2, J1.SHELL1, J1.SHELL2, J1.SHELL3, J1.SHELL4, R3.2
unnamed: C68.1 (+), U18.2 (INTVCC)
unnamed: D2.1 (DO), D3.4 (DI)
unnamed: D6.2 (A), R12.2
unnamed: D7.2 (A), R15.2
unnamed: D8.2 (A), R25.2
unnamed: D9.2 (A), R27.2
unnamed: D14.2 (A), R41.2
unnamed: D15.2 (A), R44.2
unnamed: D3.1 (DO), D18.4 (DI)
unnamed: D18.1 (DO), D19.4 (DI)
unnamed: D19.1 (DO), D20.4 (DI)
unnamed: D20.1 (DO), D21.4 (DI)
unnamed: D21.1 (DO), D22.4 (DI)
unnamed: D22.1 (DO), D23.4 (DI)
unnamed: J1.A5 (CC1), R4.1
unnamed: J1.B5 (CC2), R5.1
unnamed: C28.1, Q1.1 (X1), R11.1
unnamed: C29.1, Q1.3 (X2), U8.30 (XIN)
unnamed: R35.1 (+), R36.2 (-), U18.1 (EN/UVLO)
unnamed: R37.1 (+), U18.6 (RFB)
unnamed: R38.1 (+), U18.8 (TC)
unnamed: R38.2 (-), R40.1 (+), U18.7 (RREF)
unnamed: R1.1, U4.6 (DO)
unnamed: R2.1, U4.10 (nIRQ)
unnamed: R11.2, U8.31 (XOUT)
unnamed: R13.2, U11.24 (nSLEEP)
unnamed: R16.2, U12.24 (nSLEEP)
unnamed: C57.1, U16.22 (1V2O)
unnamed: R28.1, U16.27 (ACTLED)
unnamed: R27.1, U16.26 (DUPLED)
unnamed: R29.1, U16.10 (EXRES1)
unnamed: R26.1, U16.25 (LINKLED)
unnamed: R20.2, U16.45 (PMODE0)
unnamed: R21.2, U16.44 (PMODE1)
unnamed: R22.2, U16.43 (PMODE2)
unnamed: R25.1, U16.24 (SPDLED)
unnamed: C59.1, U16.20 (TOCAP)
unnamed: C52.1, R19.2, U16.30 (XI/CLKIN), Y1.1
unnamed: C53.1, R19.1, U16.31 (XO), Y1.3
unnamed: C63.2, R32.2
unnamed: R42.2, U20.24 (nSLEEP)
unnamed: R45.2, U21.24 (nSLEEP)

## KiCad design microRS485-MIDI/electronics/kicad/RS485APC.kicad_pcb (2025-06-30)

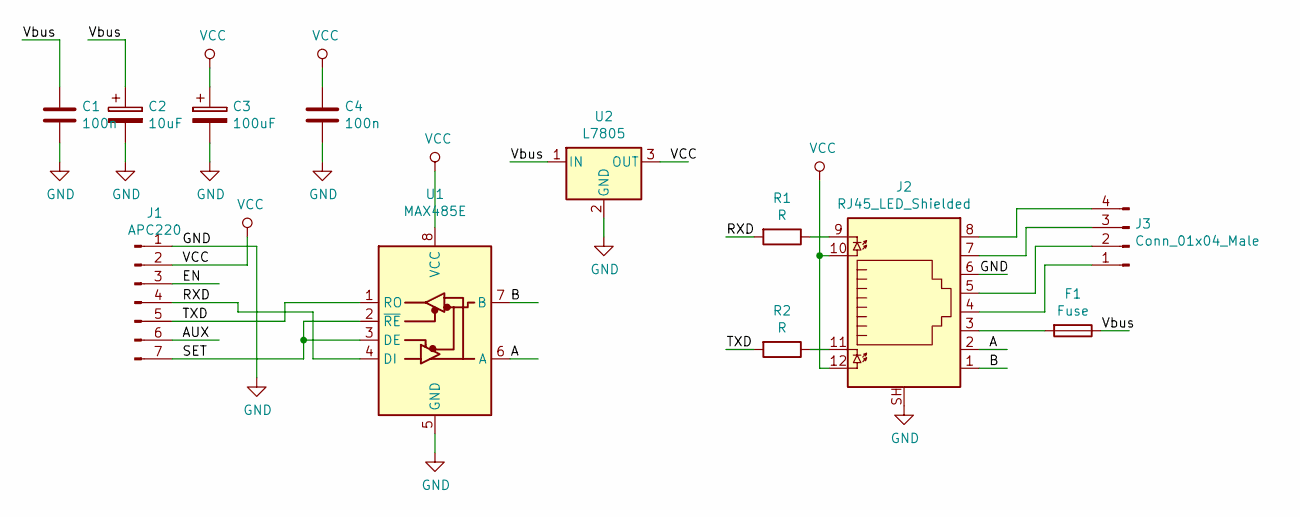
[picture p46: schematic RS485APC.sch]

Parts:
C1, C4: 100n; C_Disc_D4.7mm_W2.5mm_P5.00mm
C2: 10uF; CP_Radial_D5.0mm_P2.50mm
C3: 100uF; CP_Radial_D5.0mm_P2.50mm
F1: Fuse; PinHeader_1x02_P2.54mm_Vertical
J1: APC220; PinHeader_1x07_P2.54mm_Vertical
J2: RJ45_LED_Shielded; RJ45_Amphenol_RJHSE538X
J3: Conn_01x04_Male; PinHeader_1x04_P2.54mm_Vertical
R1, R2: R; R_Axial_DIN0207_L6.3mm_D2.5mm_P7.62mm_Horizontal
U1: MAX485E; DIP-8_W7.62mm
U2: L7805; TO-220-3_Vertical

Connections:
/A: J2.2, U1.6 (A)
/AUX: J1.6
/B: J2.1, U1.7 (B)
/EN: J1.3
/RXD: J1.4, R1.2, U1.4 (DI)
/SET: J1.7, U1.2 (~RE), U1.3 (DE)
/TXD: J1.5, R2.2, U1.1 (RO)
/Vbus: C1.1, C2.1, F1.1, U2.1 (IN)
GND: C1.2, C2.2, C3.2, C4.2, J1.1, J2.6, J2.SH, U1.5 (GND), U2.2 (GND)
unnamed: F1.2, J2.3
unnamed: J2.4, J3.1
unnamed: J2.5, J3.2
unnamed: J2.7, J3.3
unnamed: J2.8, J3.4
unnamed: J2.9, R1.1
unnamed: J2.11, R2.1
VCC: C3.1, C4.1, J1.2, J2.10, J2.12, U1.8 (VCC), U2.3 (OUT)

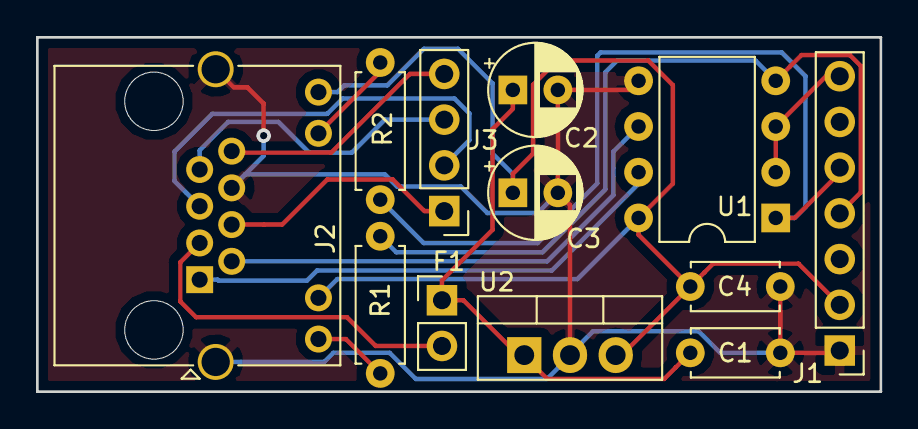
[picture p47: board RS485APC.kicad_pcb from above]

Board: 2 copper layers, 46.9 x 19.7 mm, 12 parts (0 on the bottom side), 15 nets.

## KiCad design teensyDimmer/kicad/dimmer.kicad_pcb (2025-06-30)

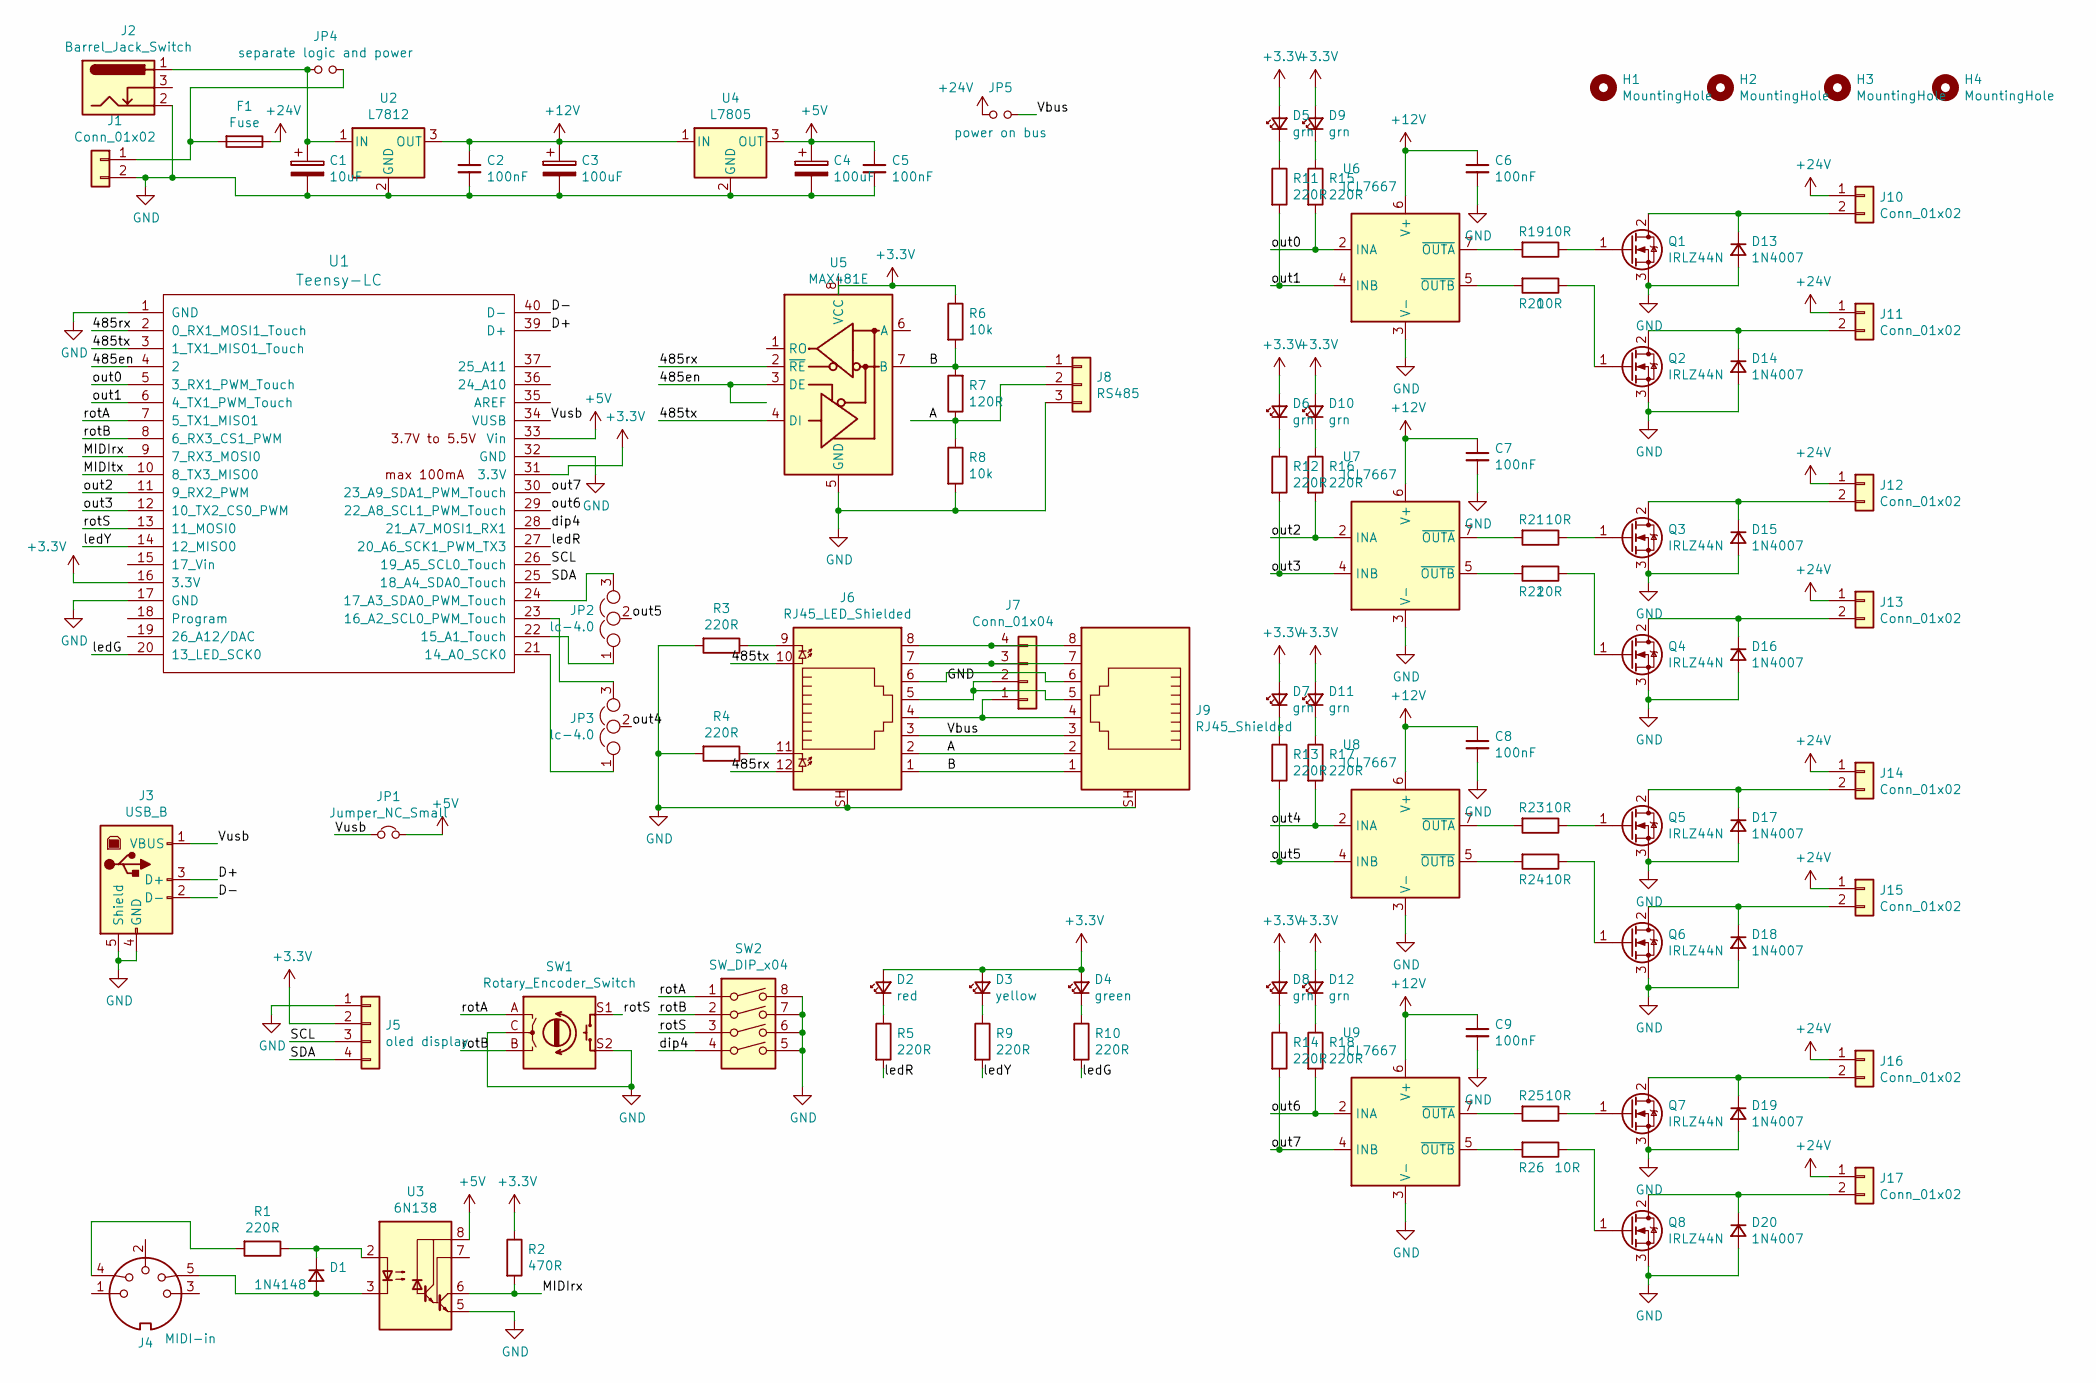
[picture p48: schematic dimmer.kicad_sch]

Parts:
C1: 10uF; CP_Radial_D5.0mm_P2.50mm
C2, C5: 100nF; C_Disc_D5.0mm_W2.5mm_P5.00mm
C3, C4: 100uF; CP_Radial_D6.3mm_P2.50mm
C6, C7, C8, C9: 100nF; C_Disc_D3.0mm_W2.0mm_P2.50mm
D1: 1N4148; D_DO-34_SOD68_P7.62mm_Horizontal
D2: red; LED_D3.0mm
D3: yellow; LED_D3.0mm
D4: green; LED_D3.0mm
D5, D6, D7, D8, D9, D10, D11, D12: grn; LED_D3.0mm
D13, D14, D15, D16, D17, D18, D19, D20: 1N4007; D_A-405_P7.62mm_Horizontal
F1: Fuse; Fuse_Bourns_MF-RHT300
H1, H2, H3, H4: MountingHole; MountingHole_3.2mm_M3
J1, J10, J11, J12, J13, J14, J15, J16, J17: Conn_01x02; PhoenixContact_MC_1,5_2-G-3.81_1x02_P3.81mm_Horizontal
J2: Barrel_Jack_Switch; BarrelJack_Horizontal
J3: USB_B; USB_A
J4: MIDI-in; PinHeader_1x05_P2.54mm_Vertical
J5: oled display; PinHeader_1x04_P2.54mm_Vertical
J6: RJ45_LED_Shielded; RJ45_Amphenol_RJHSE538X
J7: Conn_01x04; PinHeader_1x04_P2.54mm_Vertical
J8: RS485; PinHeader_1x03_P2.54mm_Vertical
J9: RJ45_Shielded; RJ45_Amphenol_RJHSE538X
JP1: Jumper_NC_Small; SolderJumper-2_P1.3mm_Bridged_RoundedPad1.0x1.5mm
JP2, JP3: lc-4.0; SolderJumper-3_P1.3mm_Bridged12_RoundedPad1.0x1.5mm
JP4: separate logic and power; PinHeader_1x02_P2.54mm_Vertical
JP5: power on bus; PinHeader_1x02_P2.54mm_Vertical
Q1, Q2, Q3, Q4, Q5, Q6, Q7, Q8: IRLZ44N; TO-220-3_Horizontal_TabUp
R1, R3, R4, R5, R9, R10, R11, R12, R13, R14, R15, R16, R17, R18: 220R; R_Axial_DIN0207_L6.3mm_D2.5mm_P7.62mm_Horizontal
R2: 470R; R_Axial_DIN0207_L6.3mm_D2.5mm_P7.62mm_Horizontal
R6, R8: 10k; R_Axial_DIN0207_L6.3mm_D2.5mm_P7.62mm_Horizontal
R7: 120R; R_Axial_DIN0207_L6.3mm_D2.5mm_P7.62mm_Horizontal
R19, R20, R21, R22, R23, R24, R25, R26: 10R; R_Axial_DIN0207_L6.3mm_D2.5mm_P7.62mm_Horizontal
SW1: Rotary_Encoder_Switch; RotaryEncoder_Alps_EC11E-Switch_Vertical_H20mm
SW2: SW_DIP_x04; DIP-8_W7.62mm
U1: Teensy-LC; Teensy_LC
U2: L7812; TO-220-3_Horizontal_TabUp
U3: 6N138; DIP-8_W7.62mm
U4: L7805; TO-220-3_Horizontal_TabUp
U5: MAX481E; DIP-8_W7.62mm
U6, U7, U8, U9: ICL7667; DIP-8_W7.62mm

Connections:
+3V3: D2.2 (A), D3.2 (A), D4.2 (A), D5.2 (A), D6.2 (A), D7.2 (A), D8.2 (A), D9.2 (A), D10.2 (A), D11.2 (A), D12.2 (A), J5.2, R2.1, R6.1, U1.16 (3.3V), U1.31 (3.3V), U5.8 (VCC)
+5V: C4.1, C5.1, JP1.2, U1.33 (Vin), U3.8 (VCC), U4.3 (OUT)
+12V: C2.1, C3.1, C6.1, C7.1, C8.1, C9.1, U2.3 (OUT), U4.1 (IN), U6.6 (V+), U7.6 (V+), U8.6 (V+), U9.6 (V+)
+24V: F1.1, J10.1, J11.1, J12.1, J13.1, J14.1, J15.1, J16.1, J17.1, JP5.1
/485tx: J6.10, U1.3 (1_TX1_MISO1_Touch), U5.4 (DI)
/A: J6.2, J8.2, J9.2, R7.1, R8.1, U5.6 (A)
/B: J6.1, J8.1, J9.1, R6.2, R7.2, U5.7 (B)
/D+: J3.3 (D+), U1.39 (D+)
/D-: J3.2 (D-), U1.40 (D-)
/MIDIrx: R2.2, U1.9 (7_RX3_MOSI0), U3.6 (VO2)
/MIDItx: U1.10 (8_TX3_MISO0)
/SCL: J5.3, U1.26 (19_A5_SCL0_Touch)
/SDA: J5.4, U1.25 (18_A4_SDA0_Touch)
/Vbus: J6.3, J9.3, JP5.2
/Vusb: J3.1 (VBUS), JP1.1, U1.34 (VUSB)
/dip4: SW2.4, U1.28 (21_A7_MOSI1_RX1)
/ledG: R10.2, U1.20 (13_LED_SCK0)
/ledR: R5.2, U1.27 (20_A6_SCK1_PWM_TX3)
/ledY: R9.2, U1.14 (12_MISO0)
/out0: R15.2, U1.5 (3_RX1_PWM_Touch), U6.2 (INA)
/out1: R11.2, U1.6 (4_TX1_PWM_Touch), U6.4 (INB)
/out2: R16.2, U1.11 (9_RX2_PWM), U7.2 (INA)
/out3: R12.2, U1.12 (10_TX2_CS0_PWM), U7.4 (INB)
/out4: JP3.2, R17.2, U8.2 (INA)
/out5: JP2.2, R13.2, U8.4 (INB)
/out6: R18.2, U1.29 (22_A8_SCL1_PWM_Touch), U9.2 (INA)
/out7: R14.2, U1.30 (23_A9_SDA1_PWM_Touch), U9.4 (INB)
/rotA: SW1.A, SW2.1, U1.7 (5_TX1_MISO1)
/rotB: SW1.B, SW2.2, U1.8 (6_RX3_CS1_PWM)
/rotS: SW1.S1, SW2.3, U1.13 (11_MOSI0)
GND: C1.2, C2.2, C3.2, C4.2, C5.2, C6.2, C7.2, C8.2, C9.2, D13.2 (A), D14.2 (A), D15.2 (A), D16.2 (A), D17.2 (A), D18.2 (A), D19.2 (A), D20.2 (A), J1.2, J2.2, J3.4 (GND), J3.5 (Shield), J5.1, J6.6, J6.SH, J8.3, J9.6, J9.SH, Q1.3 (S), Q2.3 (S), Q3.3 (S), Q4.3 (S), Q5.3 (S), Q6.3 (S), Q7.3 (S), Q8.3 (S), R3.2, R4.2, R8.2, SW1.C, SW1.S2, SW2.5, SW2.6, SW2.7, SW2.8, U1.1 (GND), U1.17 (GND), U1.32 (GND), U2.2 (GND), U3.5 (GND), U4.2 (GND), U5.5 (GND), U6.3 (V-), U7.3 (V-), U8.3 (V-), U9.3 (V-)
unnamed: C1.1, J2.1, JP4.1, U2.1 (IN)
unnamed: D1.1 (K), R1.1, U3.2 (C1)
unnamed: D1.2 (A), J4.5, U3.3 (C2)
unnamed: D2.1 (K), R5.1
unnamed: D3.1 (K), R9.1
unnamed: D4.1 (K), R10.1
unnamed: D5.1 (K), R11.1
unnamed: D6.1 (K), R12.1
unnamed: D7.1 (K), R13.1
unnamed: D8.1 (K), R14.1
unnamed: D9.1 (K), R15.1
unnamed: D10.1 (K), R16.1
unnamed: D11.1 (K), R17.1
unnamed: D12.1 (K), R18.1
unnamed: D13.1 (K), J10.2, Q1.2 (D)
unnamed: D14.1 (K), J11.2, Q2.2 (D)
unnamed: D15.1 (K), J12.2, Q3.2 (D)
unnamed: D16.1 (K), J13.2, Q4.2 (D)
unnamed: D17.1 (K), J14.2, Q5.2 (D)
unnamed: D18.1 (K), J15.2, Q6.2 (D)
unnamed: D19.1 (K), J16.2, Q7.2 (D)
unnamed: D20.1 (K), J17.2, Q8.2 (D)
unnamed: F1.2, J1.1, JP4.2
unnamed: J4.4, R1.2
unnamed: J6.4, J7.1, J9.4
unnamed: J6.5, J7.2, J9.5
unnamed: J6.7, J7.3, J9.7
unnamed: J6.8, J7.4, J9.8
unnamed: J6.9, R3.1
unnamed: J6.11, R4.1
unnamed: JP2.1, U1.22 (15_A1_Touch)
unnamed: JP2.3, U1.24 (17_A3_SDA0_PWM_Touch)
unnamed: JP3.1, U1.21 (14_A0_SCK0)
unnamed: JP3.3, U1.23 (16_A2_SCL0_PWM_Touch)
unnamed: Q1.1 (G), R19.1
unnamed: Q2.1 (G), R20.1
unnamed: Q3.1 (G), R21.1
unnamed: Q4.1 (G), R22.1
unnamed: Q5.1 (G), R23.1
unnamed: Q6.1 (G), R24.1
unnamed: Q7.1 (G), R25.1
unnamed: Q8.1 (G), R26.1
unnamed: R19.2, U6.7 (~OUTA)
unnamed: R20.2, U6.5 (~OUTB)
unnamed: R21.2, U7.7 (~OUTA)
unnamed: R22.2, U7.5 (~OUTB)
unnamed: R23.2, U8.7 (~OUTA)
unnamed: R24.2, U8.5 (~OUTB)
unnamed: R25.2, U9.7 (~OUTA)
unnamed: R26.2, U9.5 (~OUTB)

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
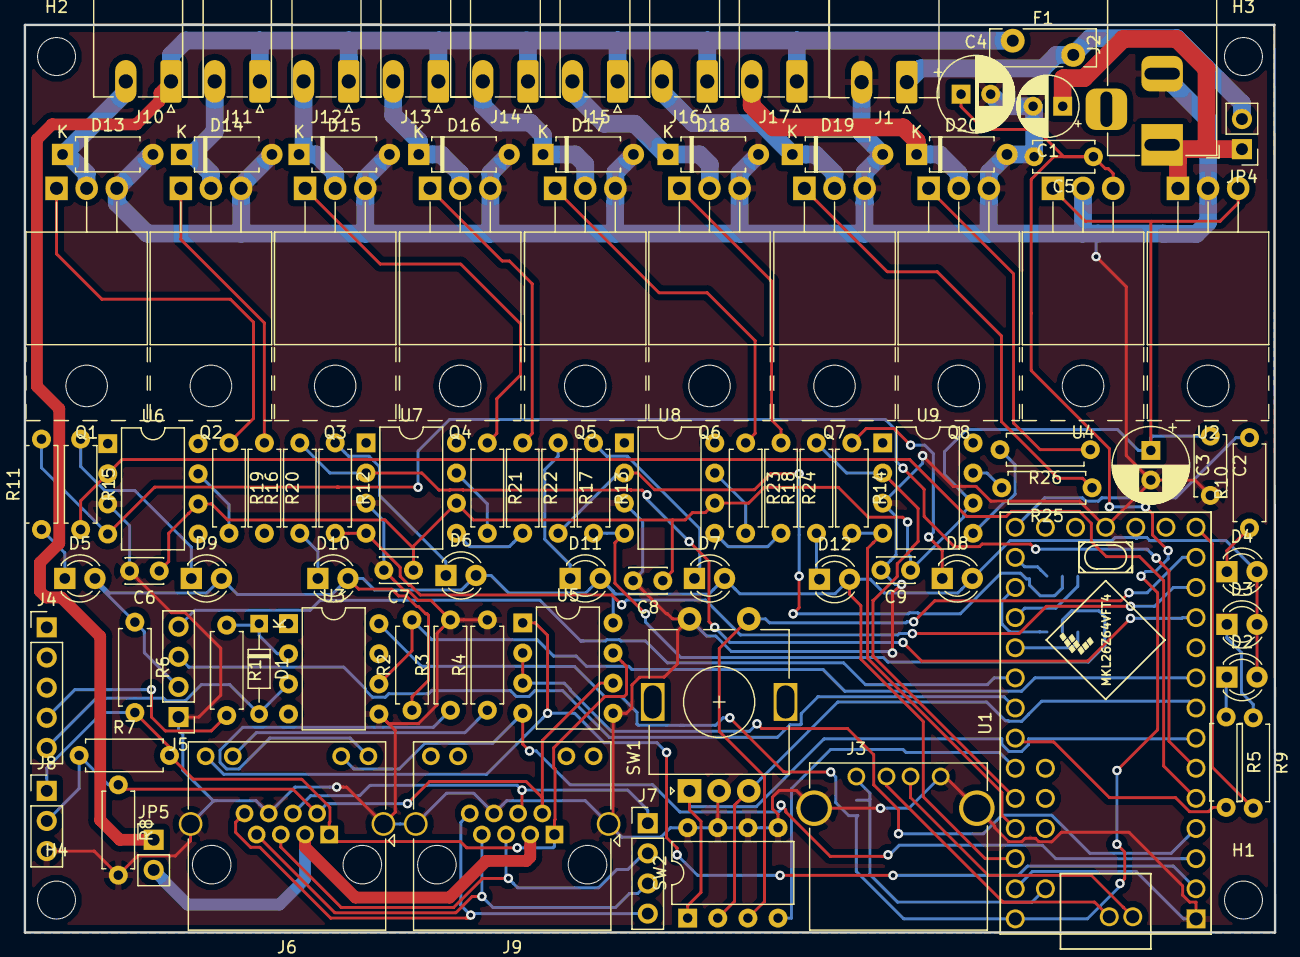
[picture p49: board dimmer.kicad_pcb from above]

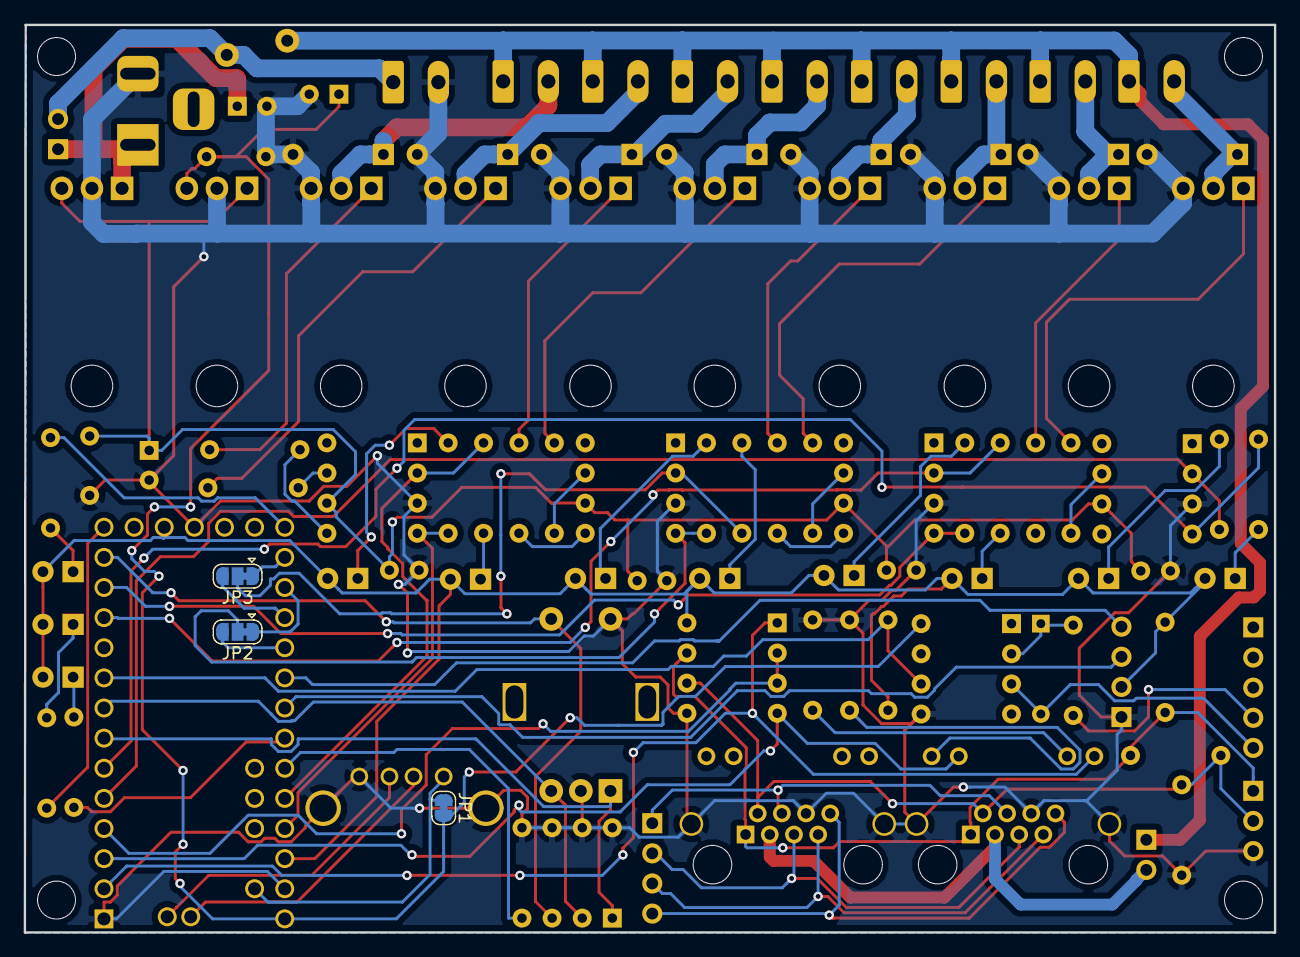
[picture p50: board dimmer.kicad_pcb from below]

Board: 2 copper layers, 105.4 x 76.5 mm, 101 parts (3 on the bottom side), 82 nets.

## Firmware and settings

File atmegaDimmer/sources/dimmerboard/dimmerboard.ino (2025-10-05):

//*****************************************************************************
// DimmerBoardTimeController project
// RS485 control board software for Dancing Man or other time based control
//
// The dimmer cards use ATmega88 controllers at 16 MHz (early choice, economical)
// They can be programmed using arduino hardware defintion for Ottantotto
// programming using an AVR-ISP such as AVR-ISP MKII or USBasp unit
//
// The baudrate can be set to 57600 but also works at 1000000 selected using dip switch 4 (OFF: 57600, ON: 1000000)
// mode (dimmer or time) can be set using dip switch 3 (OFF: dimmer, OND: time)
// address [0..3] is set with switches 1 and 2
//
// This software can be put into a Dimmerboard. It will control each of the
// eight outputs as follows:
// + Normally the output is turned off.
// + When a message (see below) is sent, the respective channel will be on for
//     a short period of time, being value*10 ms. Because this has been designed
//     to work with MIDI signals, it is considered that the value lies between
//     0 and 127 (including).
// + If a new command is sent while the output is still on, the old command
//   is discarded and the new one will be executed (and the output will be
//   on for value*10 ms, counting from the time the new command was sent)
// + Value 0 will immediately turn off the output (this is a direct consequence
//   of the previous rule).
// + Value 127 is special: it will leave the output on until a new command is sent.
//
// This software expects a dynamixel-compatible protocol. A message is composed as follows:
// 0xFF   'header'
// 0xFF
// 0x??   'ID'         : board address (NOT <<4, as in earlier versions)
// 0x04   'Data length': number of bytes to follow
// 0x03   'Write'      : command
// 0x??   'Parameter 1': channel; 0..7: channel, >7: broadcast (all channels of the dimmer board)
// 0x??   'Parameter 2': value (turn-on time, in 10ms/increment (so value=31 gives a pulse of 310 ms)
// 0x??   'Checksum'   : ~(ID + 0x04 + 0x03 + channel + value) (~=bitwise NOT)
//
// Example: FF FF 01 04 03 05 08 DA will turn on output 5 on board 04 for 80 ms.
//
// address and mode jumpers are only checked at startup.
//
// Pinning Atmel Controller     |Arduino
// PD0 Serial RXD   (RS485)     |0
// PD1 Serial TXD   (RS485)     |1
// PD2 Send/Receive (RS485)     |2
// PD3 LED D1                   |3
// PD4 Adr 1                    |4
// PD5 Adr 2                    |5
// PD6 Adr 3                    |6
// PD7 Adr 4                    |7
// PB0 channel0                 |8
// PB1 channel1                 |9
// PB2 channel2                 |10
// PB3 channel3                 |11
// PB4 LED D2                   |12
// PB5 LED D3                   |13 (LED)
// PC0 channel4                 |A0
// PC1 channel5                 |A1
// PC2 channel6                 |A2
// PC3 channel7                 |A3
// PC4 I2C SDA                  |A4 (SDA)
// PC5 I2C SCL                  |A5 (SCL)
//*****************************************************************************
#include <EEPROM.h>
// as low baudrate in previous systems 57600 has been used, 1000000 is necessary for (for example) Dynamixel Servos
#define BAUDRATE_LOW 115200
#define BAUDRATE_HIGH 1000000
//#define ORDER_RYG (1)  // soldered LEDs might end up in different order
#define ORDER_YGR (1)
//#define ORDER_GYR (1)
//#define LED_ADDRESS_COUNT (1)

int basenote; // we store this in EEPROM so it can be changed by special RS485 message
int eeprom_address = 1;   // just a spot. Pick a new one after 100000 cycles :)
#define BASE_CHANNEL 0 // midi channel
// Uncomment the following to change the behaviour regarding 'broadcast' channels (i.e. everything not in the channel slot the system is assigned to
//#define BROADCAST (1)



// mode 0: time control (valves)
// mode 1: pwm  control (LED dimmer)
int mode = 0; // but changed in the void setup()

//////////////////////////////////////////////////
#ifdef ORDER_GYR
#define LED_GREEN 13
#define LED_YELLOW 3
#define LED_RED 12
#elif ORDER_RYG
#define LED_GREEN 12
#define LED_YELLOW 13
#define LED_RED 3
#elif ORDER_YGR
#define LED_GREEN 13
#define LED_YELLOW 3
#define LED_RED 12
#else
#warning "LED ORDER NOT DEFINED"
#endif

// Channel definitions:
#define FET0PORT PORTB
#define FET1PORT PORTB
#define FET2PORT PORTB
#define FET3PORT PORTB
#define FET4PORT PORTC
#define FET5PORT PORTC
#define FET6PORT PORTC
#define FET7PORT PORTC
#define FET0PIN 0
#define FET1PIN 1
#define FET2PIN 2
#define FET3PIN 3
#define FET4PIN 0
#define FET5PIN 1
#define FET6PIN 2
#define FET7PIN 3
///////////////////////////////////////////////////////////////////////////////////////////
// Usefull utility functions to work with ports outside the standard Arduino functions
// outb(), inb(), inw(), outw(), BV(), sbi(), cbi()
// as inheritance from WinAVR style programming
#define outb(addr, data)  addr = (data)
#define inb(addr)     (addr)
#define outw(addr, data)  addr = (data)
#define inw(addr)     (addr)
#define BV(bit)     (1<<(bit))
#define cbi(reg,bit)  reg &= ~(BV(bit))
#define sbi(reg,bit)  reg |= (BV(bit))
#define limit(number,boundary) ( ((number)>(boundary))?(boundary):( ((number)<(-boundary))?(-boundary):(number)) )
#define limit2(number,min,max) ( ((number)>(max))?(max):( ((number)<(min))?(min):(number)) )
#define toggle(port,nr) if(port & 1<<nr) cbi(port,nr); else sbi(port,nr)
#define FALSE (0)
#define TRUE (1)
///////////////////////////////////////////////////////////////////////////////////////////
//
#define DYNAMIXEL_BUFFER_SIZE (128) // make sure it never overflows.
#define N_CHANNELS (8) // number of LED/PWM/Valve channels

/* dim curve taken from http://www.kasperkamperman.com */
const unsigned char dim_curve[] PROGMEM = {
  0,   1,   1,   2,   2,   2,   2,   2,   2,   3,   3,   3,   3,   3,   3,   3,
  3,   3,   3,   3,   3,   3,   3,   4,   4,   4,   4,   4,   4,   4,   4,   4,
  4,   4,   4,   5,   5,   5,   5,   5,   5,   5,   5,   5,   5,   6,   6,   6,
  6,   6,   6,   6,   6,   7,   7,   7,   7,   7,   7,   7,   8,   8,   8,   8,
  8,   8,   9,   9,   9,   9,   9,   9,   10,  10,  10,  10,  10,  11,  11,  11,
  11,  11,  12,  12,  12,  12,  12,  13,  13,  13,  13,  14,  14,  14,  14,  15,
  15,  15,  16,  16,  16,  16,  17,  17,  17,  18,  18,  18,  19,  19,  19,  20,
  20,  20,  21,  21,  22,  22,  22,  23,  23,  24,  24,  25,  25,  25,  26,  26,
  27,  27,  28,  28,  29,  29,  30,  30,  31,  32,  32,  33,  33,  34,  35,  35,
  36,  36,  37,  38,  38,  39,  40,  40,  41,  42,  43,  43,  44,  45,  46,  47,
  48,  48,  49,  50,  51,  52,  53,  54,  55,  56,  57,  58,  59,  60,  61,  62,
  63,  64,  65,  66,  68,  69,  70,  71,  73,  74,  75,  76,  78,  79,  81,  82,
  83,  85,  86,  88,  90,  91,  93,  94,  96,  98,  99,  101, 103, 105, 107, 109,
  110, 112, 114, 116, 118, 121, 123, 125, 127, 129, 132, 134, 136, 139, 141, 144,
  146, 149, 151, 154, 157, 159, 162, 165, 168, 171, 174, 177, 180, 183, 186, 190,
  193, 196, 200, 203, 207, 211, 214, 218, 222, 226, 230, 234, 238, 242, 248, 255,
};


/* PWM_FREQ
  Ideally, choose a multiple of ONE_OVER_TIME_UNIT; this will increas accuracy (because we
  are doing an integer division PWM_FREQ/ONE_OVER_TIME_UNIT somewhere).
*/
#define PWM_FREQ (200)

/* PWM_RESOLUTION
  How many steps do we have in the pwm?
  Higher number: more resolution in intensity.
  Lower number: faster PWM possible.
  Don't make this one larger than 128, because that will overflow
  our signed ints! (128 itself is allowed, though)
*/
#define PWM_RESOLUTION (125)

/* ONE_OVER_TIME_UNIT
  how many 'time units' go in 1 second? i.e. if we give 10 here, the variable _time in
  ProcessNewCommand denotes the rise time in 10'ths of a seconds. If we put 1000 here, it
  denotes the rise time in ms.
*/
#define ONE_OVER_TIME_UNIT (10)

/* This struct contains everything we need to know about a channel. Using this, we can,
  each time step, calculate the new current_intensity. We use signed ints here as
  'fixed point' variables so that we have a higher accuracy/resolution in the ramp-up. */
typedef struct {
  //////////////////////////////////////
  // 'current state'; The two variables below are needed to keep the current
  // state of the PWM channel

  /* current_intensity: We use the highest byte as the desired duty-cycle,
     i.e. DutyCycle = highbyte(current_intensity) / RESOLUTION. */
  signed int current_intensity;

  /* counter: Each channel has its own counter. The value of counter is
     always compard with current_intensity; if counter < current_intensity,
     the LED is turned on. The reaason why we use different counters for
     each channel is that it makes that not PWM-channels are reset at the
     same time. This minimizes calculation jitter (we don't need to re-calculate
     the current_intensity for all the channels during one pulse), and it also
     distributes the current because not all channels are on at the same time.
     counter runs from 0 till (PWM_RESOLUTION-1).
  */
  unsigned char counter;


  /////////////////////////////////////
  // 'Command memory'; the two variables below store stuff that is needed
  // to process the ramp-command
  /* final_intensity:  We use the highest byte as the desired duty-cycle,
     i.e. DutyCycle = highbyte(current_intensity) / RESOLUTION. */
  signed int final_intensity;

  /* increment: How much the current_intensity should be incremented each PWM_FREQ 'th
     second. May be negative. */
  signed int increment;

  /* used to store lookup-table corrected intensity value */
  unsigned char corrected_intensity;
} LedChannelInfo;

typedef enum {
  WaitingForFirstHeaderByte,
  WaitingForSecondHeaderByte,
  WaitingForIDByte,
  WaitingForDataLengthByte,
  WaitingForRestOfMessage
} e_receive_state;

e_receive_state ReceiveState = WaitingForFirstHeaderByte;

/* This struct contains everything we need to know about a channel. Using this, we can,
  each time step, calculate the new current_intensity. We use signed ints here as
  'fixed point' variables so that we have a higher accuracy/resolution in the ramp-up. */
typedef struct {
  //////////////////////////////////////
  // 'current state'; The two variables below are needed to keep the current
  // state of the time controlled channel

  /* duration: the number of samples (typically with a sample time of 10 ms = 100 Hz)
     that the channel should be on. This should be set by the ProcessNewCommand function. */
  int duration;

  /* timeOn: The number of samples that the channel has been on. This is read&set by
     the update function. */
  int timeOn;

  /* newCommand: Is set to true when a new command is issued. This allows the CommandUpdate()
     to properly handle new commands (sometimes, it can be unclear that a new command was
     issued). */
  unsigned char newCommand; // actually a bool

  /* on: Boolean that tells if the FET is on (if so, CommandUpdate() should process it) */
  unsigned char on; // actually a bool
} ChannelInfo;

ChannelInfo channel[N_CHANNELS]; // The information
LedChannelInfo ledChannel[N_CHANNELS]; // The information

//////////////////////////////////////////////////
// global variables
unsigned char c;
unsigned char addressBuffer = 0;
unsigned char DataLengthBuffer = 0;
unsigned char NumberOfDataBytesReceived = 0;
unsigned char Data[DYNAMIXEL_BUFFER_SIZE];
unsigned char checksumBuffer = 0;
unsigned char boardAddress;

void setup() {
  pinMode(LED_YELLOW, OUTPUT);
  pinMode(LED_RED, OUTPUT);
  pinMode(LED_GREEN, OUTPUT);

  outb(DDRB, 0x3F);
  outb(PORTB, 0x3F); // Output fets off

  outb(DDRC, 0x0F); // General purpose input / ADC
  outb(PORTC, 0x0F);

  outb(DDRD, 0x0C); // only SR as output -- and LED yellow
  outb(PORTD, 0xF8);

  sbi(PORTD, 3);
  cbi(PORTD, 2); // set RS485 to listen
  sbi(PORTD, 0); //pullup?

  //
  // now checking dip switches:
  boardAddress = 4 * BASE_CHANNEL + digitalRead(4) + 2 * digitalRead(5);
  mode = digitalRead(6);
  if (digitalRead(7)) Serial.begin(BAUDRATE_LOW); else Serial.begin(BAUDRATE_HIGH);
  //
  if (mode)LedControlInit(); else ControlInit();

  EEPROM.get(eeprom_address, basenote);
  //if (basenote < 0 || basenote > 120) basenote = BASE_NOTE;
#ifdef LED_ADDRESS_COUNT
  blinkRed(basenote);
#endif
  TCCR2A = 0; // no ocr or pwm
  TCCR2B = 4; //1<<CS22 | 0<<CS21 | 0<<CS20 -- for clock div 64
  TIMSK2 = 1 << TOIE2; // enable timer 1 interrupt
  TCNT2 = 0xce; // 5 kHz
}

void blinkRed(int n) {
  for (int i = 0; i < n; i++) {
    digitalWrite(LED_RED, LOW);
    delay(100);
    digitalWrite(LED_RED, HIGH);
    delay(100);
  }
}

void loop() {
  if (Serial.available() > 0) {
    c = Serial.read();
    switch (ReceiveState)
    {
      case WaitingForFirstHeaderByte:
        if (c == 0xFF) // first byte of header
        {
          ReceiveState = WaitingForSecondHeaderByte;
        }
        break;
      case WaitingForSecondHeaderByte:
        if (c == 0xFF)
        {
          if (digitalRead(LED_YELLOW)) digitalWrite(LED_YELLOW, LOW); else digitalWrite(LED_YELLOW, HIGH);
          // toggle(PORTB, 5); // yellow LED to show bus communication
          ReceiveState = WaitingForIDByte;
        } else ReceiveState = WaitingForFirstHeaderByte;
        break;
      case WaitingForIDByte:
        // store byte
        addressBuffer = c;
        checksumBuffer = c;
        ReceiveState = WaitingForDataLengthByte;
        break;
      case WaitingForDataLengthByte:
        DataLengthBuffer = c;
        NumberOfDataBytesReceived = 0;
        checksumBuffer += c;
        ReceiveState = WaitingForRestOfMessage;
        break;
      case WaitingForRestOfMessage:
        if (NumberOfDataBytesReceived < DYNAMIXEL_BUFFER_SIZE)
        {
          Data[NumberOfDataBytesReceived] = c;
        } // otherwise, we would have buffer overflow
        checksumBuffer += c;
        NumberOfDataBytesReceived++;
        if (NumberOfDataBytesReceived == DataLengthBuffer)
        {
          // We're finished receiving the message, so process it
          if (addressBuffer == boardAddress)
          {
            // Then it is meant for this board
            // Check if the data is correct by means of checksum.
            // Also, if we had a buffer overflow, we know for sure that the
            // data is invalid (because we only stored part of it, so in that case we
            // should not process it either. It would have been a faulty command anyway).
            if ( (checksumBuffer & 0xFF) == 0xFF && NumberOfDataBytesReceived < DYNAMIXEL_BUFFER_SIZE)
            {
              // Then the data is correct
              if (digitalRead(LED_GREEN)) digitalWrite(LED_GREEN, LOW); else digitalWrite(LED_GREEN, HIGH);
              ProcessData(DataLengthBuffer, Data);
            } else
            {
              //toggle(PORTB, 4); // checksum error
              if (digitalRead(LED_RED)) digitalWrite(LED_RED, LOW); else digitalWrite(LED_RED, HIGH);
            }
          }

          ReceiveState = WaitingForFirstHeaderByte;
        }
        break;
    }
  }
}

ISR(TIMER2_OVF_vect) {
  TCNT2 = 0xf6; // reload timer at 5kHz
  static unsigned char counter = 0;
  if (mode) LedControlUpdate();
  // 100 Hz loop
  else {
    if ( ++counter == 25)
    {
      counter = 0;
      ControlUpdate();
    }
  }
}

/*********************************************************
  Checks what data is in the message and acts accordingly.
*/
void ProcessData(unsigned char DataLengthBuffer, unsigned char* Data)
{
  // We only support one type of message, being a 'write' message (command 0x03) for a
  // channel to turn itself on for some time.
  // DataLengthBuffer should be 4.
  // Command  is in Data[0];
  // Channel  is in Data[1];
  // Time     is in Data[2];
  // Checksum is in Data[3]; (and it is valid).


  if (Data[0] == 0x03) {
    if (DataLengthBuffer != 0x04) return; // Todo: should we light a led to indicate this??
    if (Data[1] >= basenote && Data[1] < basenote + N_CHANNELS) {
      if (mode) ProcessDimmerCommand(constrain(Data[1] - basenote, 0, 127), Data[2], 1);
      else ProcessNewCommand(constrain(Data[1] - basenote, 0, 127), Data[2]);
    }
  }
  else if (Data[0] == 0x05) {
    if (DataLengthBuffer != 0x0B) return; // this is a group message, 1 + 8 + 2 bytes
    if (Data[1] == basenote) { // then it's for this board: 0, 8, 16, 24, 32, etc...
      for (int i = 0; i < N_CHANNELS; i++) {
        if (mode) ProcessDimmerCommand(i - basenote, Data[i + 2], 1);
        else ProcessNewCommand(i - basenote, Data[i + 2]);
      }
    }
  }
  else if (Data[0] == 0x06) {
    if (DataLengthBuffer != 0x04) return;
    if (Data[1] == 0) {
      if (Data[2] >= 0 && Data[2] < 120) {
        digitalWrite(LED_RED, LOW);
        basenote = Data[2];
        EEPROM.put(eeprom_address, basenote);

        delay(200);
        digitalWrite(LED_RED, HIGH);
      }
    }
  }
}
/******************************************************************
  void ControlInit(void)

  Initializes the ChannelInfo variables
*/
void ControlInit(void)
{
  int i;
  ChannelInfo *c;
  for (i = 0; i < N_CHANNELS; i++)
  {
    c = &(channel[i]);
    c->duration = 0;
    c->timeOn = 0;
  }
}


/******************************************************************
  void ProcessNewCommand( unsigned char _channel, unsigned char _time)

  Sets up the system such that this command is handled.
  - _channel should be 0..(N_CHANNELS-1).
    Any number higher than that will cause ALL channels to do
    this command. This allows for a general OFF. As a convention,
    use channel = 0x0F = 15 for this.
  - _time is in samples. If the function ControlUpdate() is called
    100 times per second (ie, ever 10 ms), the channel will be turned
    on for _time*10 ms.
    Exception: a _time of 127 will turn the FET on forever (until a new command is issued)

    If a new command is sent while the channel was still on, the old
    command is canceled and the new command is executed (so, from that time
    on, the FET will be turned on for _time * 10 ms).
    Use a _time = 0 to instantaneously turn off the FET.
*/
void ProcessNewCommand( unsigned char _channel, unsigned char _time)
{
  if (_channel < N_CHANNELS)
  {
    ChannelInfo *c;
    c = &(channel[_channel]);

    c->duration = _time;
    c->newCommand = TRUE;
  } else
  {
#ifdef BROADCAST
    // Then it is a broadcast
    for (int i = 0; i < N_CHANNELS; i++) ProcessNewCommand(i, _time);
#endif
  }
}



/******************************************************************
  void ControlUpdate(void)

  This function should be called regularly, for example 100 times per second.
*/
void ControlUpdate(void)
{
  unsigned char i;
  ChannelInfo *c;

  for (i = 0; i < N_CHANNELS; i++)
  {
    c = &(channel[i]);
    if ( c -> newCommand ) // Then we should instantiate a command
    {
      c -> newCommand = FALSE;

      if (c->duration == 0) // special case, we need to turn off the FET
      {
        TurnOff(i);
        c -> on = FALSE;
      } else
      {
        // Turn it on
        TurnOn(i);
        c -> timeOn = 0;
        c -> on = TRUE;
      }
    } else if (c -> on)
    {
      // Then the channel is on, so process it

      if (c->duration != 127) // if it _is_ 127, we should never turn off the led
      {
        if (++(c->timeOn) >= c->duration)
        {
          // Then turn it off
          TurnOff(i);
          c -> duration = 0; // Not really needed, but more beautiful
          c -> timeOn = 0;   // Not really needed, but more beautiful
          c -> on = FALSE;
        }
      }
    }
  }
}


/******************************************************************
  Turns on the specific channel
*/
void TurnOn(unsigned char channel)
{
  switch (channel)
  {
    case 0: cbi(FET0PORT, FET0PIN); break;
    case 1: cbi(FET1PORT, FET1PIN); break;
    case 2: cbi(FET2PORT, FET2PIN); break;
    case 3: cbi(FET3PORT, FET3PIN); break;
    case 4: cbi(FET4PORT, FET4PIN); break;
    case 5: cbi(FET5PORT, FET5PIN); break;
    case 6: cbi(FET6PORT, FET6PIN); break;
    case 7: cbi(FET7PORT, FET7PIN); break;
    default: break;// ERROR
  }
}

/******************************************************************
  Turns off the specific channel
*/
void TurnOff(unsigned char channel)
{
  switch (channel)
  {
    case 0: sbi(FET0PORT, FET0PIN); break;
    case 1: sbi(FET1PORT, FET1PIN); break;
    case 2: sbi(FET2PORT, FET2PIN); break;
    case 3: sbi(FET3PORT, FET3PIN); break;
    case 4: sbi(FET4PORT, FET4PIN); break;
    case 5: sbi(FET5PORT, FET5PIN); break;
    case 6: sbi(FET6PORT, FET6PIN); break;
    case 7: sbi(FET7PORT, FET7PIN); break;
    default: break;// ERROR
  }
}

/******************************************************************
  void LedControlInit(void)

  Initializes the ChannelInfo variables
*/
void LedControlInit(void)
{
  int i;
  LedChannelInfo *c;
  for (i = 0; i < N_CHANNELS; i++)
  {
    c = &(ledChannel[i]);
    c->current_intensity = 0;
    c->counter = i * (PWM_RESOLUTION / N_CHANNELS); // Make sure that the counters are all out-of-sync (see .h file for explanation)
    c->final_intensity = 0;
    c->increment = 0;
    c->corrected_intensity = 0;
  }
}
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

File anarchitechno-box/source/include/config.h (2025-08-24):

#pragma once
//#define DEBUG (1)
// note that this definition has its consequences in the main.cpp and also in action.h (where
// each action mapping is given)
// the animation tracks are added in the file animation.cpp, the number of steps in the
// header file animation.h (so check those before compiling.)
//////////////////////////////////////////////////////////////////////////////////////////////
//#define ANIMAL_LOVE
//#define KLARA
//#define ANIMALTRONIEK_KREEFT (1)
//#define ANIMALTRONIEK_VIS (1)
//#define ANIMALTRONIEK_SCHILDPAD (1)
//#define SCUBA (1)
//#define AMI (1)
//#define LUMI (1)
//#define DESKLIGHT (1)
#define EXPERIMENT (1)
//////////////////////////////////////////////////////////////////////////////////////////////

#ifdef DESKLIGHT
// the Waveshare motors
//#define USE_DDSM (1)
#define USE_STS (1)
#define BOARD_V2 (1)
#define USE_OLED (1)
#define USE_CRSF (1)
#define CRSF_CHANNEL_OFFSET 3 //experimental offset needed to remap correctly... 
#define NUM_CHANNELS 16
const int saveValues[NUM_CHANNELS] = { 127, 0, 0, 127, 0, 0, 0, 0, 0, 0, 0, 0, 0, 0, 0, 0};
#endif

#ifdef EXPERIMENT
//#define USE_DDSM (1)
//#define USE_STS (1)
//#define ROBOTIS (1)
#define BOARD_V1 (1)
#define USE_RS485 (1)
#define RS485_BAUD 57600
#define USE_OLED (1)
#define USE_CRSF (1)
#define CRSF_CHANNEL_OFFSET 3 //experimental offset needed to remap correctly... 
#define NUM_CHANNELS 16
const int saveValues[NUM_CHANNELS] = { 127, 0, 0, 127, 0, 0, 0, 0, 0, 0, 0, 0, 0, 0, 0, 0};
#endif

#ifdef ANIMAL_LOVE
#define BOARD_V2 (1)
#define NUM_CHANNELS 16
const int saveValues[NUM_CHANNELS] = { 127, 127, 0, 0, 0, 0, 0, 0, 0, 0, 0, 0, 0, 0, 0, 0};
//#define USE_9685 (1)
//#define USE_9635 (1)
#define USE_MOTOR (1)
//#define USE_CROSS_MIXING (1)
#define USE_SPEEDSCALING (1)
#define LOW_SPEED 130  // was 60 used for scaling in the cross-mix function
#define HIGH_SPEED 160 // was 90  
// when no scaling used:
#define MAX_SPEED 50

// for serial output on the RJ45 socket, goes to APC220 RF interface
#define USE_RS485 (1)
#define RS485_BAUD 9600
#define BUFFER_PASSTHROUGH 9  // message size, reduce to relevant portion
// for the OLED. check the &Wire or &Wire1 (for the latest board). Also check the resolution
#define USE_OLED (1)
// only use the encoder when these pins are not used for controlling separate motors
//#define USE_ENCODER (1)
// for the audio module. Typically we use both (a sample and loop player)
//#define USE_AUDIO (1)

// RF is either CRSF or (older) APC220 radio
#define USE_CRSF (1)
#define CRSF_CHANNEL_OFFSET 3 //experimental offset needed to remap correctly... 

#define KEYPAD_CHANNEL 3
#define VOLUME_CHANNEL 4
#define SWITCH_CHANNEL 5 //second switch channel will be +1, next up + 2 and + 3

#define ANIMATION_KEY (30) // set the correct animation key here. should be in last of 4 in order to NOT be recorded
#define STEPS 967 
#endif


#ifdef LUMI
#define BOARD_V2 (1)
//#define USE_9685 (1)
//#define USE_9635 (1)
//#define USE_MOTOR (1)
//#define USE_CROSS_MIXING (1)
#define USE_SPEEDSCALING (1)
#define LOW_SPEED 60  // used for scaling in the cross-mix function
#define HIGH_SPEED 90 
// when no scaling used:
#define MAX_SPEED 50
#define USB_JOYSTICK
#define NUM_CHANNELS 16
const int saveValues[NUM_CHANNELS] = { 127, 127, 127, 127, 0, 127, 127, 0, 0, 127, 0, 0, 0, 0, 0, 0};
// for serial output on the RJ45 socket, goes to CAT5 ethernet cable
//#define USE_RS485 (1)
//#define RS_485_BAUD 57600
// for the OLED. check the &Wire or &Wire1 (for the latest board). Also check the resolution
#define USE_OLED (1)
// only use the encoder when these pins are not used for controlling separate motors
//#define USE_ENCODER (1)
// for the audio module. Typically we use both (a sample and loop player)
#define USE_AUDIO (1)

// RF is either CRSF or (older) APC220 radio
#define USE_CRSF (1)
#define CRSF_CHANNEL_OFFSET 3 //experimental offset needed to remap correctly... 

//#define KEYPAD_CHANNEL 3
//#define VOLUME_CHANNEL 3
#define SWITCH_CHANNEL 12 //second switch channel will be +1, next up + 2 and + 3

//#define ANIMATION_KEY (32) // set the correct animation key here. should be in last of 4 in order to NOT be recorded
//#define STEPS 1

#define NUM_TRACKS 15
const String tracklist[NUM_TRACKS] = 
{
  "/mp3/01-int.mp3",
  "/mp3/02-dro.mp3",
  "/mp3/03-maz.mp3",
  "/mp3/04-sco.mp3",
  "/mp3/05-spi.mp3",
  "/mp3/06-pat.mp3",
  "/mp3/07-moe.mp3",
  "/mp3/08-wal.mp3",
  "/mp3/09-poo.mp3",
  "/mp3/10-cer.mp3",
  "/mp3/11-opt.mp3",
  "/mp3/12-kar.mp3",
  "/mp3/13-and.mp3",
  "/mp3/14-mid.mp3",
  "/mp3/15-ora.mp3",
};
#define NUM_SAMPLES 6
const String samplelist[NUM_SAMPLES] = 
{
  "/mp3/01-alm.mp3",
  "/mp3/02-ang.mp3",
  "/mp3/03-slp.mp3",
  "/mp3/04-mov.mp3",
  "/mp3/05-noo.mp3",
  "/mp3/06-yes.mp3"
};

#endif
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

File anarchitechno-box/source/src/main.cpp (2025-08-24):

// this controlbox can use multiple radio systems.
// on th RF spot there is place for an
// APC220. using RX and Tx
// link RF-set to gnd and write 'RD' or 'WR'
// with a specific configuration string
// for BetaFPV/ELRS/CrossFire you can send and
// receive a CRSF string. make sure remote and receiver
// are paired (see betafpv manual), flashed with 
// firmware v3.4.3 or up (same for Tx and Tx). Set 
// packet rate to 333 (or100), switches to 16/2 ch and telemetry to 1:128
// 
// TODO: for the animaltroniek the air or driving edition have not been 
// added yet.
//
// resources:
// https://arduino-pico.readthedocs.io/en/latest/index.html
// edit the config.h to set the specifics for a used robot or vehicle
#include <Arduino.h> // the EarlPhilHower Arduino port of Pico SDK
#include <Wire.h>    // the I2C communication lib for the display, PCA9685 etc
#include <config.h>  // the specifics for the controlled robot or vehicle
#include <hardware/watchdog.h>
// hardware on every board: the relay sockets
#include <PicoRelay.h>
PicoRelay relay;
// Feed MIDI activity
uint8_t levels[8];

/// MIDI functions (USB MIDI, see Adafruit config in platformio.ini)
#include <MIDI.h>
#include "Adafruit_TinyUSB.h"
// USB MIDI object
Adafruit_USBD_MIDI usb_midi;
// Create a new instance of the Arduino MIDI Library,
// and attach usb_midi as the transport.
MIDI_CREATE_INSTANCE(Adafruit_USBD_MIDI, usb_midi, MIDI);
/////////// function prototypes //////////////////
void handleNoteOn(byte channel, byte pitch, byte velocity);
void handleNoteOff(byte channel, byte pitch, byte velocity);
void handlePitchBend(byte channel, int bend);
void handleControlChange(byte channel, byte control, byte value);
//////////// That's the USB MIDI bit ////////////////////////////

///// now for the multi channel PWM timing
#include <PWMhelper.h>
PWMHelper pwm;
////////////////////

#include "AWG.h"

AWG awg(16000, 255, 1000);

// and the bookkeeping for the polyphony
// Voice structure
struct Voice {
  int note = -1;        // MIDI note number, -1 = free
  int pin;              // GPIO pin used
  bool active = false;  
};
// Only 5 pins → 5 voices
int voicePins[3] = { 26, 28,24};
Voice voices[3];
// Global modulation + pitchbend state
int16_t pitchBendValue = 0;   // -8192…+8191
int pitchBendRange = 2;       // semitones up/down
uint8_t modulationValue = 64; // 0…127
//////////////////////////////////////////////////////////////////////////////////////////////
// the one and only global channel array containing the received values from RF
// at present 14 of the 16 channels are used. Enter the save values (FAILSAFE) in these arrays
//                               0  1  2  3  4  5  6  7  8  9 10 11 12 13 14 15
int channels[NUM_CHANNELS] =   { 0, 0, 0, 0, 0, 0, 0, 0, 0, 0, 0, 0, 0, 0, 0, 0};
// for most of the exoot:        X  Y nb kp vo sw sw sw sw
//////////////////////////////////////////////////////////////////////////////////////////////

#include <OledMenu.h>

// global menu instance
OledMenu menu;



// running modes
#define IDLE 0
#define ACTIVE 1
#define PLAYBACK 2

// for triggers or tracks on DFRobot players. Note: they have to be installed
// otherwise the initialisation will hang
#ifdef USE_AUDIO
DFRobot_DF1201S player1,player2;
SoftwareSerial player1port(7, 6);
SoftwareSerial player2port(17, 16);  //RX  TX ( so player TX, player RX)
void processAudio();
#endif
// matching function between keypad/button register and call-back check from action list
// currently using one button channel (characters '0' and higher)
// and 32 switch positions (in 4 bytes)
bool getRemoteSwitch(char button) {
  if((button >='0' && button<='9') || button=='*' || button=='#'){ // check keypad buttons
    #ifdef KEYPAD_CHANNEL
    if(channels[KEYPAD_CHANNEL] == button) return true;
    #endif
  }
  #ifdef SWITCH_CHANNEL
  else if(button >=0 && button < 8) {
    if((channels[SWITCH_CHANNEL]) & 1<<button) return true;
  }
  else if(button >=8 && button < 16) {
    if((channels[SWITCH_CHANNEL+1]) & 1<<(button-8)) return true;
  }
  else if(button >=16 && button < 24) {
    if((channels[SWITCH_CHANNEL+2]) & 1<<(button-16)) return true;
  }
  else if(button >=24 && button < 32) {
    if((channels[SWITCH_CHANNEL+3]) & 1<<(button-24)) return true;
  }
  #endif
  return false;
}
// radio communication: for now either the CRSF (ELRS) or the (old) APC220 434 MHz system
#ifdef USE_CRSF
#include "CRSF.h"
CRSF crsf;
#else
#include "Radio.h"
#endif
//////////////////////////////////////////////////////////////////////////////////////////
// and here the program starts
//////////////////////////////////////////////////////////////////////////////////////////
void setup() {
  Serial.begin(115200);
  pinMode(LED_BUILTIN, OUTPUT);
 

relay.begin();

  // radio on Serial2: CRSF or APC RF:
#ifdef USE_CRSF
  crsf.begin();
#else
  RFinit();
  RFsetSettings(2);
#endif
// and now start up the channel buffer!
  for (int n = 0; n < NUM_CHANNELS; n++) {
        channels[n] = saveValues[n];
  }
  watchdog_enable(200, 1);  // 100 ms timeout, pause_on_debug = true

  menu.begin();


}


void loop() {
  static int mode = IDLE;  // check the status
  static bool startedUp = false; // to avoid responding to the inital timeout (zero) 
// the following are important to make sure the brakes are switched on after a second of inactivity
  static bool brakeState = 1;
  static unsigned long brakeTimer;
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

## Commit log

2025-06-30 added files of former projects
    [RS485APC.kicad_pcb, RS485APC.sch, box.stl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]
2025-08-24 added anarchitechno box project
    [RS485APC.kicad_pcb, RS485APC.sch, anarchytechnobox.kicad_pcb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]
2025-09-03 added tapperdiaper and picture
    [tapperdaiper.scad]
2025-09-03 RP2350 initial commit
    [FET.kicad_sch, RP2350BMCU.kicad_sch, TwoIsolatedFETs.kicad_sch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]
2025-09-18 Large intermediate schematic push. Remaining todos are on frontpage.
    [FET.kicad_sch, RP2350BMCU.kicad_sch, TwoIsolatedFETs.kicad_sch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]
2025-09-21 Stijn in de Trein
    [anarchytechnobox.kicad_pcb, anarchytechnobox.kicad_sch, eth_w5500.kicad_sch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]
2025-09-21 meer Stijn in de Trein
    [RP2350BMCU.kicad_sch, TwoIsolatedFETs.kicad_sch, anarchytechnobox.kicad_pcb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]
2025-09-21 nog meer trein
    [anarchytechnobox.kicad_pcb, anarchytechnobox.kicad_sch]
2025-09-21 trein trein trein
    [RP2350BMCU.kicad_sch, anarchytechnobox.kicad_sch, dcdc_flyback.kicad_sch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]
2025-09-21 choo choooooo
    [RP2350BMCU.kicad_sch, RS485.kicad_sch, anarchytechnobox.kicad_sch]
2025-09-21 100mbit ethernet jack
    [eth_w5500.kicad_sch]
2025-09-21 IPROPI comments on H-bridge
    [hbridge.kicad_sch]
2025-09-22 3.3V 1A regulator on high & low side
    [RP2350BMCU.kicad_sch, dcdc_flyback.kicad_sch]
2025-09-22 Layout drivers updated, more vias
2025-09-24 Re-added 1.1V regulator. Removed 3.3VDDA for Ethernet. Increased clearances on layout a bit..
    [RP2350BMCU.kicad_sch, dcdc_flyback.kicad_sch, eth_w5500.kicad_sch]
2025-09-24 Provision for backup DC/DC in case flyback doesn't work...
    [T_Wurth_WE-FB-EP13_16.36.step, dcdc_flyback.kicad_sch]
2025-09-24 Resized PCB with mounts at 125x125mm (suitable for 140mm PC fan), 4-pin fan connector added, changed 3.3VP to 5.0VP
    [TwoIsolatedFETs.kicad_sch, anarchytechnobox.kicad_sch, dcdc_flyback.kicad_sch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]
2025-09-24 MIDI input using autosensing TRS midi jack
    [MIDI.kicad_sch, anarchytechnobox.kicad_sch]
2025-10-05 added updated arduino sources for previous (atmega88) dimmer and RS485 interface
    [RS485.kicad_sch, dimmerbox.scad, dimmerbox.stl]
2025-10-05 sorry-accidently deleted these, no idea why
    [RS485.kicad_sch]
2025-10-09 Edwin's Connector Library
2025-10-09 Midi connector, ethernet connector imported with easyeda importer
2025-10-09 Schematic & PCB changes: - Cleaned up unnecessary electrolytic input capacitor flyback - Removed dual diode rectification on 5V, increased output capacitors - Feedback resistors DC/DCs set, enlarged 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
    [MIDI.kicad_sch, RP2350BMCU.kicad_sch, RS485.kicad_sch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]
2025-10-09 Midi output buffer
    [MIDI.kicad_sch]
2026-02-04 - Thermische berekening DRV8245 vs losse transistors - DRV8245 package gecorrigeerd naar TSSOP-28 - Layout aangepast om grotere package te passen - 1x GND output per kanaal - Waarschijnlijk geen 140m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
    [RP2350BMCU.kicad_sch, RS485.kicad_sch, anarchytechnobox.kicad_sch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]
2026-02-06 - Logo Robot Theater lab - UART connector - RF antenne clearance aangepast - Reset/interrupt pins ethernet aangesloten
    [MIDI.kicad_sch, RP2350BMCU.kicad_sch, anarchytechnobox.kicad_sch]
2026-03-25 BOM nagelopen, bestelklaar.
    [MIDI.kicad_sch, RP2350BMCU.kicad_sch, RS485.kicad_sch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]
2026-03-25 10k W5500 on RSVD pin
    [TwoIsolatedFETs.kicad_sch, eth_w5500.kicad_sch]
2026-03-25 PCB DRC lijkt oke
